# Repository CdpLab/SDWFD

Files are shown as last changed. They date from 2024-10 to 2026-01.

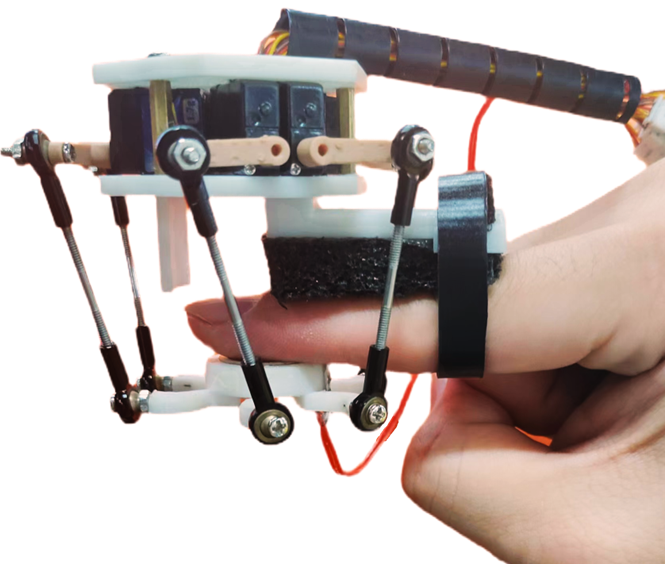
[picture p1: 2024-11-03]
picture/fig2b3.png

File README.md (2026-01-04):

<h1 align="center">Design and Evaluation of a 6-DoF Wearable Fingertip Device for Haptic Shape Rendering</h1>
<div align=center> 
Dapeng Chen, Da Yu, Yi Ding, Haojun Ni, Lifeng Zhu, Hong Zeng, Zhong Wei, Jia Liu, Aiguo Song 

Nanjing University of Information Science and Technology

---
</div>
CAD model, bill of materials and detailed manufacturing instructions, as well as its inverse kinematics and control code.The following two images show the CAD structural diagram and prototype of the device.
<div align=center>
Image text     Image text
</div>

The CAD structural diagram and prototype of the fingertip haptic device, including (A) mobile platform, (B) rocker arm, (C) fixed plate, (D) stop plate, (E) rigid link, (F) static platform, (G) steering engine, (H) rotating ball head, and (I) thin film pressure sensor.

## The CAD folder contains the assembly and various parts designed by our device.

Static platform: made of resin using 3D printing; Outer circle diameter: 48mm.

Mobile platform: made of resin using 3D printing; Outer circle diameter: 44mm, disc diameter: 22mm.

Rocker arm: Made of resin using 3D printing. Arm length: 13mm. Note: In the CAD folder, rocker arm 2 is used for 3D printing and comes with threads. And rocker arm 1 is only used for CAD display.

Rotating ball head: made of aluminum alloy.

Rigid link: made of aluminum alloy.

Screws and nuts: made of aluminum alloy.

Screw post: Made of brass.

Steering engine: Size: 16 × 17 × 6.2 mm³; mass: 17 g; model: SP017A-1; producer: DW Hobby; country: China.

Thin film pressure sensor: diameter: 20 mm; model: RP-C18.3-ST; producer: RunesKee; country: China.

## Installation process

First, install the steering engines onto the static platform. There are six square holes on the static platform to fix the rectangular prism protruding from the side of the steering engine and enhance its stability. Next, install the screw post at the corresponding position on the static platform. Then, install another static platform above the six steering engines, and securely connect two static platforms to the steering engines using screws and nuts. There is a circular hole designed on the static platform for the connection wire of the steering engine to pass through. Subsequently, the mobile platform and rigid link were installed, and the rotating ball head was pre installed in the rigid link. Connect the mobile platform to the rigid link through screws and nuts, with the screws passing through the rotating ball head. The other end of the rigid link is also connected to the rocker arm using this method, while the other end of the rocker arm is connected to the steering engine.

## Code
In the code section, we shared the code for the control, inverse kinematics, steering engine drive module, and membrane pressure sensor of the device. Among them, "FSR" is the code for the thin film pressure sensor, "control" is the code for device control, "inverse" is the code for inverse kinematics, and "pcA9685" is the code for the steering engine drive module.

## Demo video
The demonstration video can be viewed through the following link: https://youtu.be/AHHCAW3EiJQ .

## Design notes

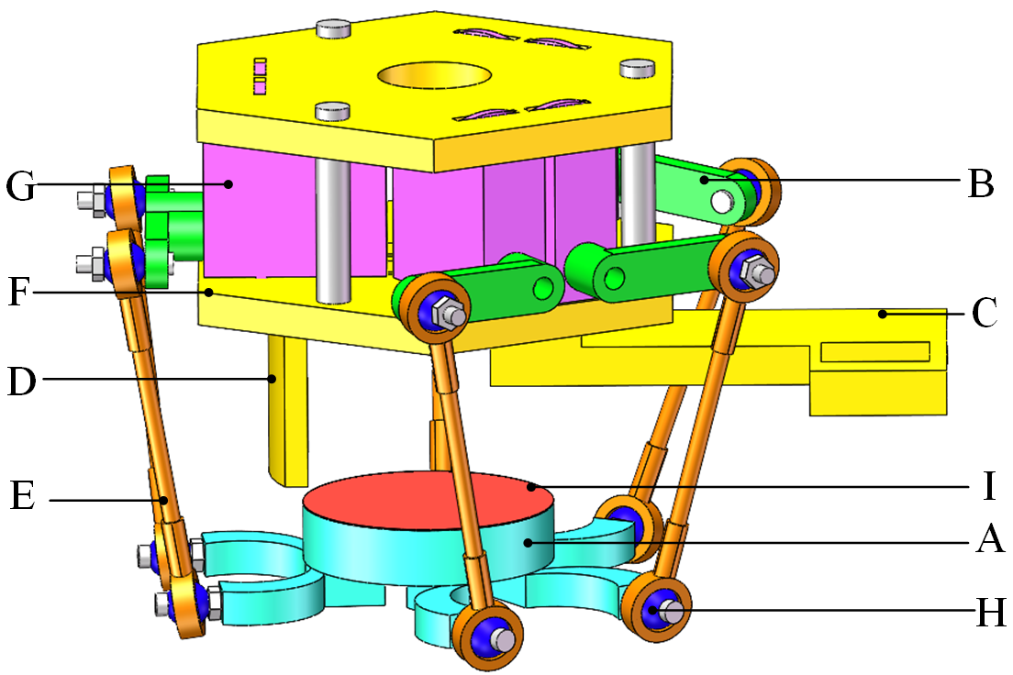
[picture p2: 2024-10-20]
picture/fig2a.png

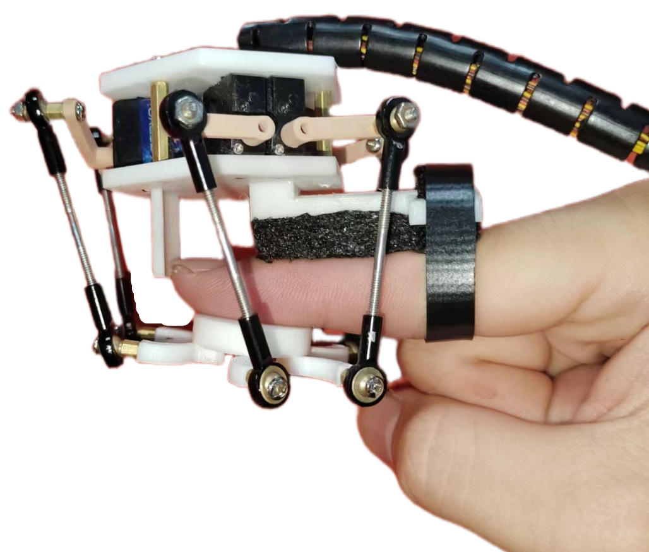
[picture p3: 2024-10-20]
picture/fig2b.png

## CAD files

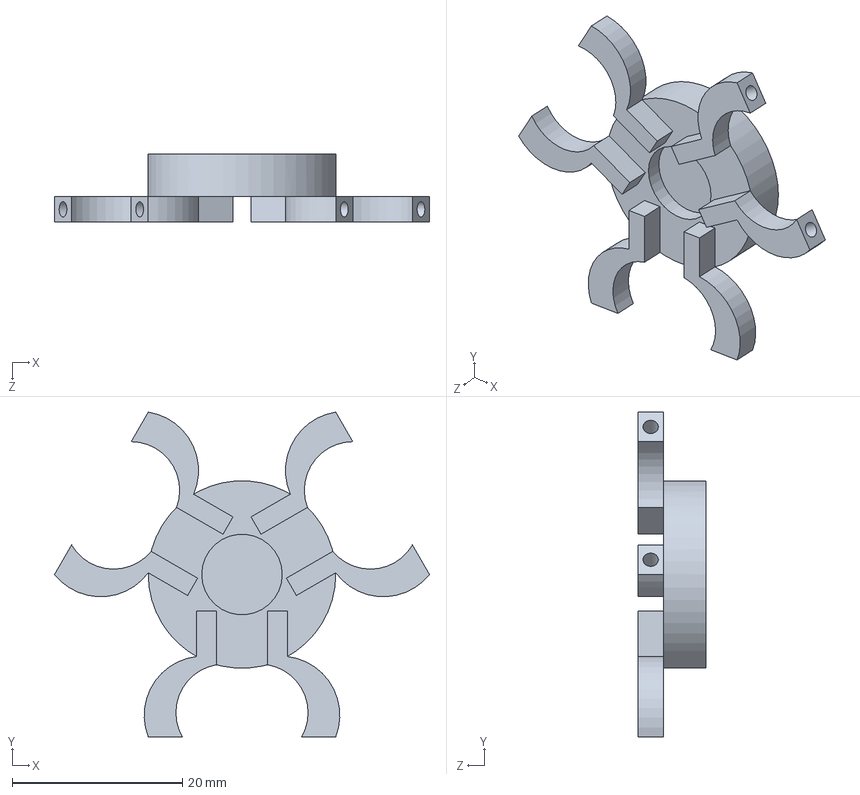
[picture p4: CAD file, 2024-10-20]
CAD/mobile platform.SLDPRT
44.0 x 38.1 x 8.00 mm

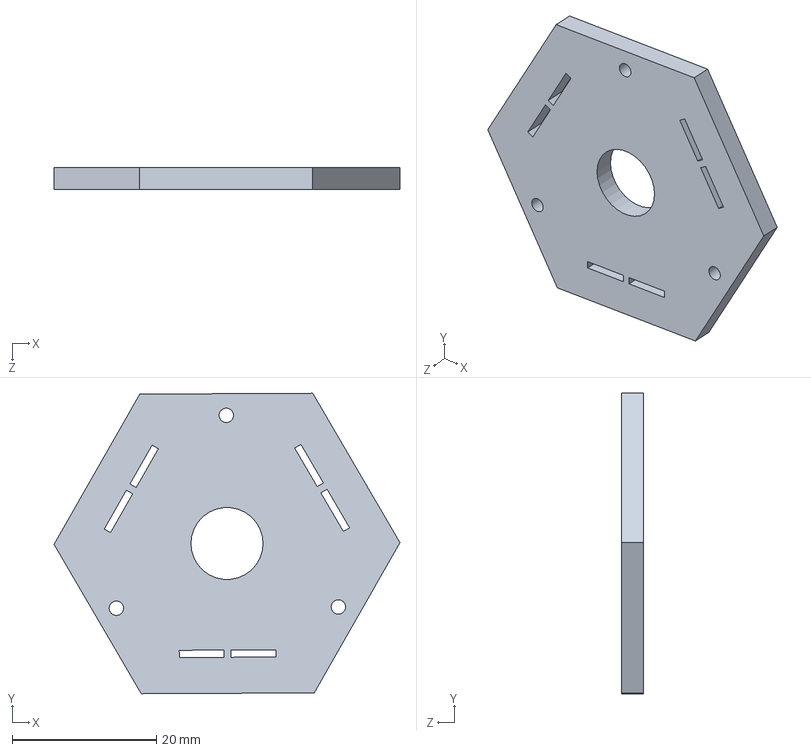
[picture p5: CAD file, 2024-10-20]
CAD/Static platform 2.SLDPRT
48.0 x 41.7 x 3.00 mm

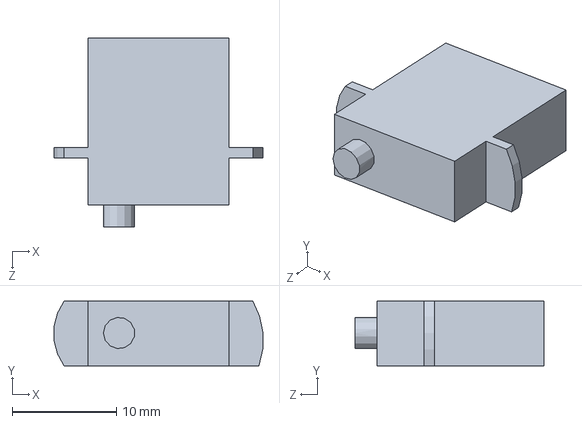
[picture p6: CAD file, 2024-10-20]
CAD/steering engine.SLDPRT
20.0 x 6.20 x 18.1 mm

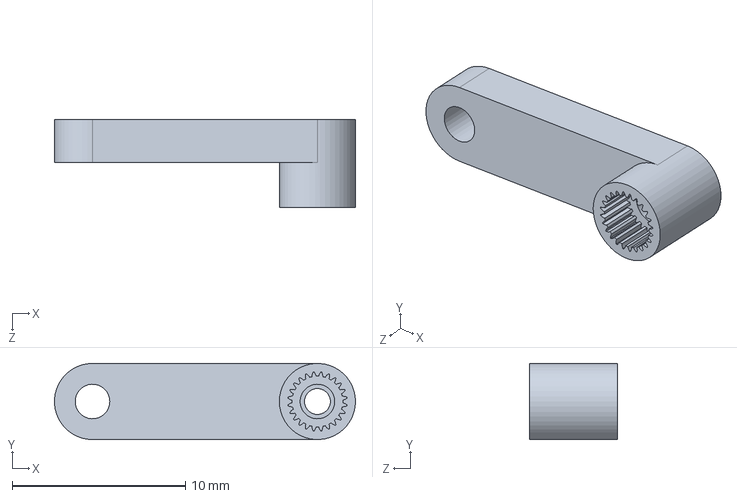
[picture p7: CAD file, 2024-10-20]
CAD/rocker arm2.SLDPRT
17.4 x 4.40 x 5.10 mm

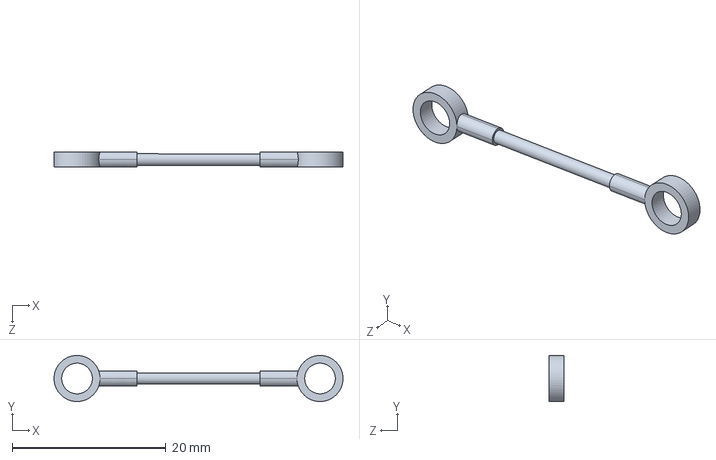
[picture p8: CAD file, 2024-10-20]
CAD/rigid link.SLDPRT
37.7 x 6.00 x 2.00 mm

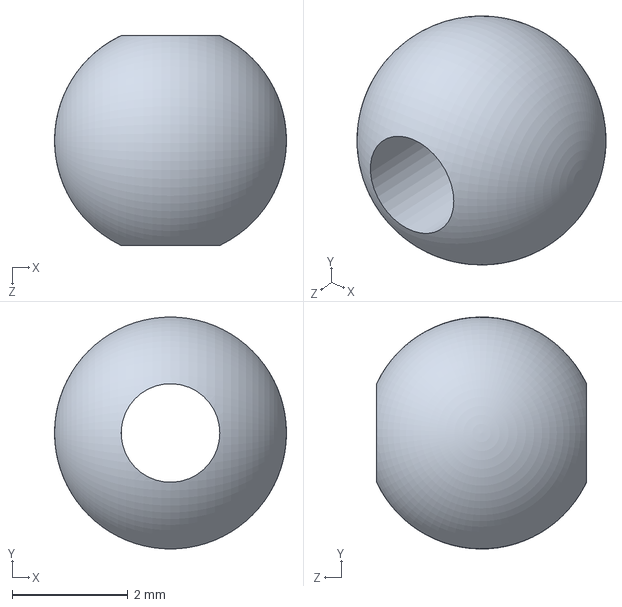
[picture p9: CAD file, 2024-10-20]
CAD/Rotating ball head.SLDPRT
4.00 x 4.00 x 3.62 mm

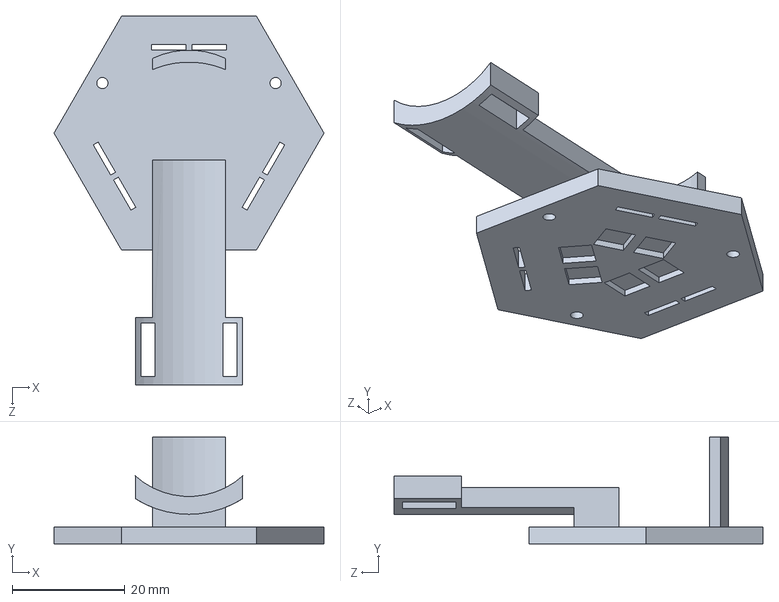
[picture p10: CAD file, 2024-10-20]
CAD/Static platform.SLDPRT
48.0 x 19.0 x 65.5 mm

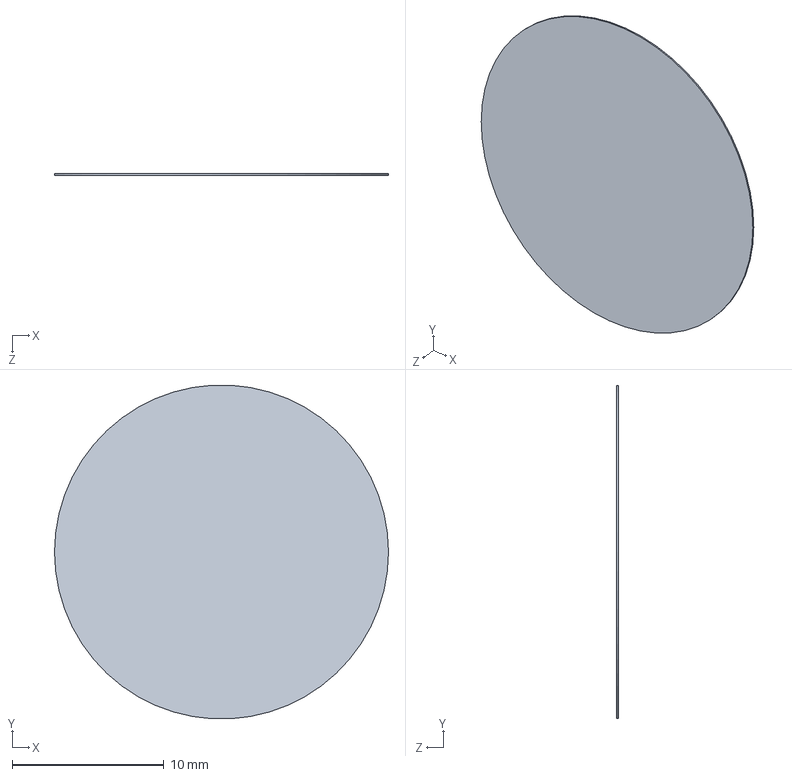
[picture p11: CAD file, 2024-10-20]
CAD/Thin film pressure sensor.SLDPRT
22.0 x 22.0 x 0.1 mm

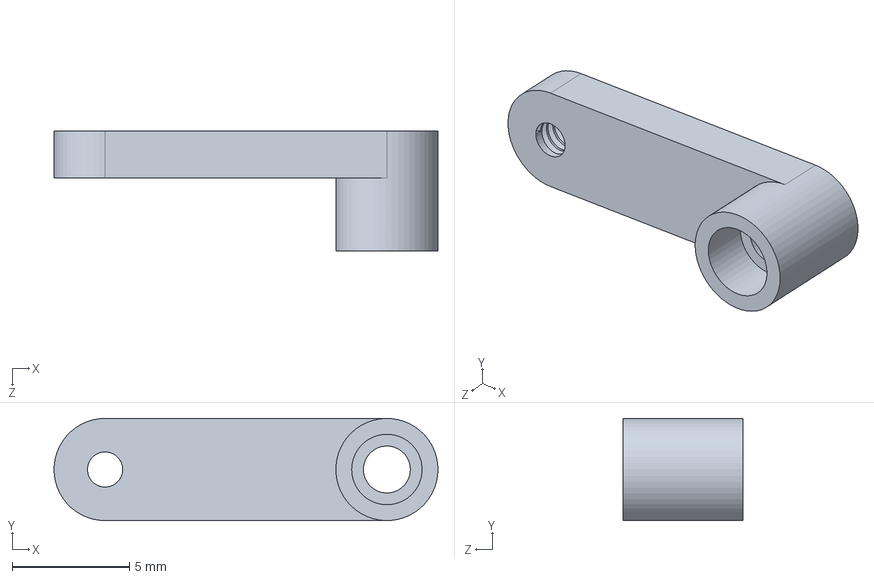
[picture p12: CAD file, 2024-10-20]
CAD/rocker arm.SLDPRT
16.4 x 4.35 x 5.10 mm

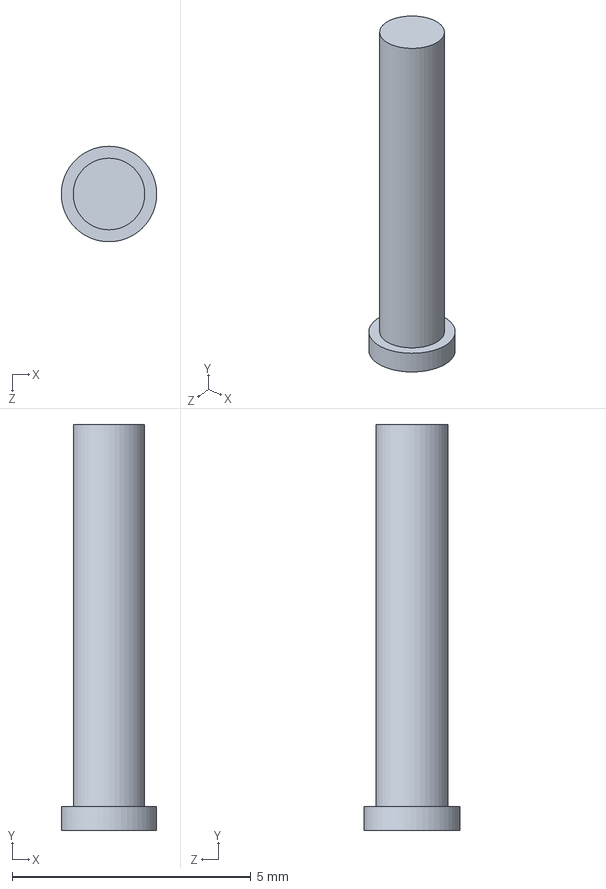
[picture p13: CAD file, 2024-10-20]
CAD/Screw 2.SLDPRT
2.00 x 8.50 x 2.00 mm

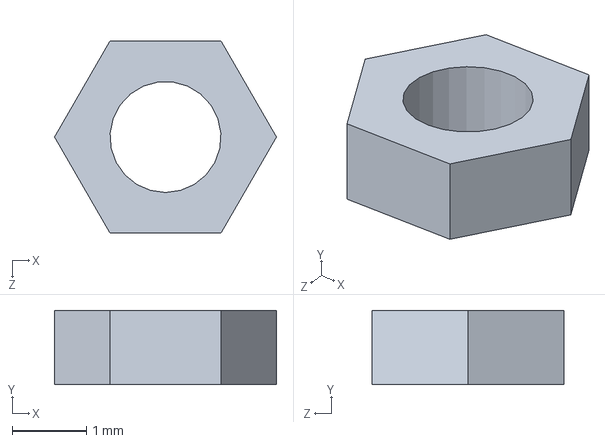
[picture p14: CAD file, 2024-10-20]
CAD/nut.SLDPRT
3.00 x 1.00 x 2.60 mm

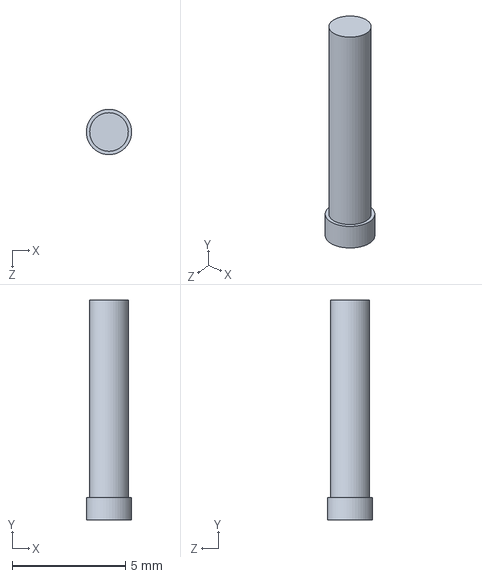
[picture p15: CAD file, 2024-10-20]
CAD/Screw.SLDPRT
2.00 x 9.70 x 2.00 mm

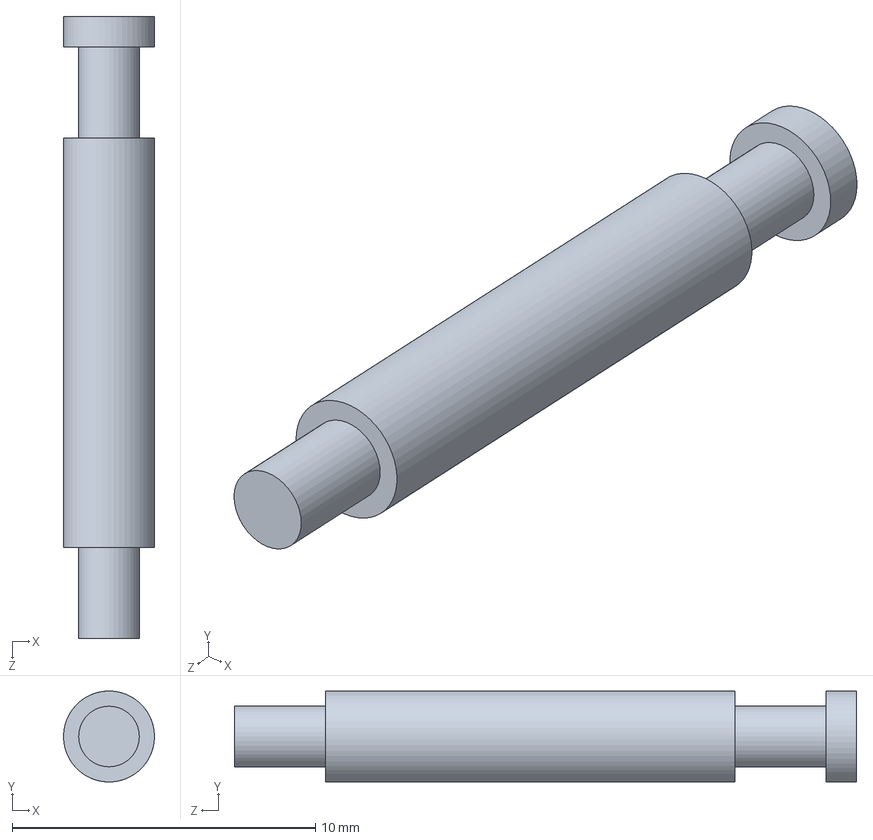
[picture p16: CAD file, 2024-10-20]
CAD/screw post.SLDPRT
3.00 x 3.00 x 20.5 mm

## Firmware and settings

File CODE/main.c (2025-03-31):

#include "system.h"
#include "SysTick.h"
#include "led.h"
#include "usart.h"
#include "FreeRTOS.h"
#include "task.h"
#include "key.h"
#include "limits.h"
#include "queue.h"
#include "serial.h"
#include "inverse.h"
#include "pca9685.h"
#include "adc.h"
#include "event_groups.h"
#include "semphr.h"
#include "limits.h"
#include "contorl.h"
//任务优先级
#define START_TASK_PRIO		1
//任务堆栈大小	
#define START_STK_SIZE 		128  
//任务句柄
TaskHandle_t StartTask_Handler;
//任务函数
void start_task(void *pvParameters);

//任务优先级
#define Inverse_task_PRIO		3
//任务堆栈大小	
#define Inverse_STK_SIZE 		128  
//任务句柄
TaskHandle_t Inversetask_Handler;
//任务函数
void Inverse_task(void *pvParameters);

//任务优先级
#define Controll_task_PRIO		4
//任务堆栈大小	
#define Controll_STK_SIZE 		50  
//任务句柄
TaskHandle_t Controlltask_Handler;
//任务函数
void Controll_task(void *pvParameters);

//任务优先级
#define Bluetooth_TASK_PRIO		2
//任务堆栈大小	
#define Bluetooth_STK_SIZE 		50  
//任务句柄
TaskHandle_t BluetoothTask_Handler;
//任务函数
void Bluetooth_task(void *pvParameters);

//任务优先级
#define FSR_TASK_PRIO		5
//任务堆栈大小	
#define FSR_STK_SIZE 		128  
//任务句柄
TaskHandle_t FSRTask_Handler;
//任务函数
void FSR_task(void *pvParameters);

#define  QUEUE_LEN    6   /* 队列的长度，最大可包含多少个消息 */
#define  QUEUE_SIZE   10   /* 队列中每个消息大小（字节） */
#define  Angel_LEN    6   /* 队列的长度，最大可包含多少个消息 */
#define  Angel_SIZE   10   /* 队列中每个消息大小（字节） */
#define  USE_CHAR  1  /* 测试字符串的时候配置为 1 ，测试变量配置为 0  */
#define PRESS_MAX	6000
#define PRESS_MIN	20
#define VOLTAGE_MIN 100
#define VOLTAGE_MAX 3300
#define KEY1_EVENT  (0x01 << 0)//设置事件掩码的位0
#define KEY2_EVENT  (0x01 << 1)//设置事件掩码的位1

QueueHandle_t Bluetooth_Queue =NULL;
QueueHandle_t Angel_Queue =NULL;
EventGroupHandle_t Event_Handle =NULL;
SemaphoreHandle_t MuxSem_Handle =NULL;
u16 adcBuffer[10];  
int main()
{
	SysTick_Init(72);
	NVIC_PriorityGroupConfig(NVIC_PriorityGroup_4);//设置系统中断优先级分组4
	LED_Init();
	KEY_Init();
	Servo_Init(50,60);
	USART1_Init(9600);
	Serial_Init();
   Adc_Init();
	//创建开始任务
    xTaskCreate((TaskFunction_t )start_task,            //任务函数
                (const char*    )"start_task",          //任务名称
                (uint16_t       )START_STK_SIZE,        //任务堆栈大小
                (void*          )NULL,                  //传递给任务函数的参数
                (UBaseType_t    )START_TASK_PRIO,       //任务优先级
                (TaskHandle_t*  )&StartTask_Handler);   //任务句柄              
    vTaskStartScheduler();          //开启任务调度
}

//开始任务任务函数
void start_task(void *pvParameters)
{
	taskENTER_CRITICAL();           //进入临界区
  /* 创建 Event_Handle */
	Event_Handle = xEventGroupCreate();
	/* 创建MuxSem */
	MuxSem_Handle = xSemaphoreCreateMutex();		
					
	xTaskCreate((TaskFunction_t )Bluetooth_task,     
                (const char*    )"Bluetooth_task",   
                (uint16_t       )Bluetooth_STK_SIZE, 
                (void*          )NULL,
                (UBaseType_t    )Bluetooth_TASK_PRIO,
                (TaskHandle_t*  )&BluetoothTask_Handler);					

		Bluetooth_Queue = xQueueCreate((UBaseType_t ) QUEUE_LEN,/* 消息队列的长度 */
                            (UBaseType_t ) QUEUE_SIZE);/* 消息的大小 */				
	
		Angel_Queue = xQueueCreate((UBaseType_t ) Angel_LEN,/* 消息队列的长度 */
                            (UBaseType_t ) Angel_SIZE);/* 消息的大小 */														
	/	
	xTaskCreate((TaskFunction_t )Inverse_task,     
                (const char*    )"Inverse_task",   
                (uint16_t       )Inverse_STK_SIZE, 
                (void*          )NULL,
                (UBaseType_t    )Inverse_task_PRIO,
                (TaskHandle_t*  )&Inversetask_Handler);					
		
	xTaskCreate((TaskFunction_t )Controll_task,     
                (const char*    )"Controll_task",   
                (uint16_t       )Controll_STK_SIZE, 
                (void*          )NULL,
                (UBaseType_t    )Controll_task_PRIO,
                (TaskHandle_t*  )&Controlltask_Handler);			
		
	xTaskCreate((TaskFunction_t )FSR_task,     
                (const char*    )"FSR_task",   
                (uint16_t       )FSR_STK_SIZE, 
                (void*          )NULL,
                (UBaseType_t    )FSR_TASK_PRIO,
                (TaskHandle_t*  )&FSRTask_Handler);							
    vTaskDelete(StartTask_Handler); //删除开始任务
    taskEXIT_CRITICAL();            //退出临界区
} 

void Bluetooth_task(void *pvParameters) {
    uint16_t t1;
    double xx[6];
    uint16_t t2 = 0;
 BaseType_t xReturn = pdPASS;/* 定义一个创建信息返回值，默认为pdPASS */
    while (1) {
        if (Serial_GetRxFlag() == 1) {
            t1 = Serial_GetRxData();
            xx[t2] = (double)t1;
            t2++;
            if (t2 == 6) { 
							xReturn = xSemaphoreTake(MuxSem_Handle,/* 互斥量句柄 */
                              portMAX_DELAY); /* 等待时间 */
							xQueueSend(Bluetooth_Queue, xx, 0);
                t2 = 0; 
        xEventGroupSetBits(Event_Handle,KEY1_EVENT); 
		    xReturn = xSemaphoreGive( MuxSem_Handle );//给出互斥量					
            }
        }
				vTaskDelay(20);
    }	
}

void Inverse_task(void *pvParameters) {
  BaseType_t xReturn = pdTRUE;/* 定义一个创建信息返回值，默认为pdTRUE */
	double rxData[6];	/* 定义一个接收消息的变量 */
	double *result;
	EventBits_t r_event;  /* 定义一个事件接收变量 */
	while(1)
    {
			  r_event = xEventGroupWaitBits(Event_Handle,  /* 事件对象句柄 */
                                  KEY1_EVENT|KEY2_EVENT,/* 接收线程感兴趣的事件 */
                                  pdTRUE,   /* 退出时清除事件位 */
                                  pdFALSE,   /* 满足感兴趣的所有事件 */
                                  portMAX_DELAY);/* 指定超时事件,一直等 */
			
     xReturn = xQueueReceive( Bluetooth_Queue,    /* 消息队列的句柄 */
								rxData,      /* 发送的消息内容 */
								portMAX_DELAY); /* 等待时间 一直等 */
		if(pdTRUE == xReturn){
			result = inv(rxData[0], rxData[1], rxData[2], rxData[3], rxData[4], rxData[5]);
//		  xQueueSend(Angel_Queue, result, 0);
			xReturn = xTaskNotify(Controll_task, /*任务句柄*/
								(uint32_t)&result, /* 发送的数据，最大为4字节 */
								eSetValueWithOverwrite );/*覆盖当前通知*/
		}
		else
			printf("数据接收出错,错误代码0x%lx\n",xReturn);
    }
}

void Controll_task(void *pvParameters) {
    BaseType_t xReturn = pdTRUE;/* 定义一个创建信息返回值，默认为pdTRUE */
	double *alpha1;
    while (1) {
			xReturn=xTaskNotifyWait(0x0,			//进入函数的时候不清除任务bit
								ULONG_MAX,	  //退出函数的时候清除所有的bit
								(uint32_t *)&alpha1,		  //保存任务通知值                       
								portMAX_DELAY);	//阻塞时间
			
//                xReturn = xQueueReceive( Angel_Queue,    /* 消息队列的句柄 */
//								alpha1,      /* 发送的消息内容 */
//								portMAX_DELAY); /* 等待时间 一直等 */
		if(pdTRUE == xReturn){
			//Servo_angle(10,60-(alpha1[0]));//-
		//Servo_angle(11,60+alpha1[1]);//+
		//Servo_angle(12,60-(alpha1[2]));
		//Servo_angle(13,60+(alpha1[3]));
		//Servo_angle(14,60-(alpha1[4])); 
		//Servo_angle(15,60+(alpha1[5]));
			servocontrol11(alpha1);
		}
		else
		{printf("数据接收出错,错误代码0x%lx\n",xReturn);}
			vTaskDelay(20);
            }
        }
				
void FSR_task(void *pvParameters) {
uint8_t state = 0;
uint16_t val = 0;
uint16_t value_AD = 0;
long PRESS_AO = 0;
uint16_t VOLTAGE_AO = 0;
BaseType_t xReturn = pdTRUE;/* 定义一个创建信息返回值，默认为pdTRUE */
	double zero[6]={0};
    while (1) {     
            value_AD = average(adcBuffer,10);	
		VOLTAGE_AO = map(value_AD, 0, 4095, 0, 3300);
		if(VOLTAGE_AO < VOLTAGE_MIN)
		{
			PRESS_AO = 0;
		}
		else if(VOLTAGE_AO > VOLTAGE_MAX)
		{
			PRESS_AO = PRESS_MAX;
		}
		else
		{
			PRESS_AO = map(VOLTAGE_AO, VOLTAGE_MIN, VOLTAGE_MAX, PRESS_MIN, PRESS_MAX);
			if (PRESS_AO>2500)
			{  xReturn = xSemaphoreTake(MuxSem_Handle,/* 互斥量句柄 */
                              portMAX_DELAY); /* 等待时间 */
				 xQueueSend(Bluetooth_Queue, zero, 0);
				 xEventGroupSetBits(Event_Handle,KEY2_EVENT);
				 xReturn = xSemaphoreGive( MuxSem_Handle);
			}
		}   
      vTaskDelay(20);		
		}
            }
        

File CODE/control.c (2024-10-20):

#include "stm32f10x.h"
#include "delay.h"
#include "sys.h"
#include "pca9685.h"
#include "usart.h"
#include "stdio.h"
#include "stdlib.h"
#include "string.h"
#include <stdarg.h>
#include "inverse.h"
#include "math.h"
#include "serial.h"
#include "MPU6050.h"
#include "inv_mpu.h"
#include "inv_mpu_dmp_motion_driver.h" 
#include "FSR.h"
#define NUM_SERVOS 6
#define INCREMENT 1.0  // 每次更新的角度增量
#define TOLERANCE 1
#define DELAY_MS 20  // 延迟时间

//差分法参数	
double timestep = 0.009;
double a0; double a1; double a2; double a3;double a4; double a5;
double omegaf;double omegai; double acci; double accf;
double tf = 0.8;
double thetai=45; double thetaf=135;
double theta0;double omega0;double acc0;
double t=0; 
int i = 0;
	
u8 state = 0;	
	
double *x;
double aa[6];
uint8_t RxData;
double val1 = 180 / 3.1415926;
int i1=0;
		int i2=0;
		double xx[24];
		uint8_t  yy[4];
    int  t1;
		double y1;
		int t2;
		double current_angles[NUM_SERVOS] = {60, 60, 60, 60, 60, 60};  // 初始化为当前角度
 int servo_pins[6] = {4, 7, 8, 11, 12, 15};			
	static u8 current_angle[6] = {0,0,0,0,0,0};	





//			for ( t = 0; t <= tf; t += timestep) {
//    thetai=60; thetaf=120;
//    omegai = 35; omegaf = 125;
//    acci = 20; accf = 40;
//    // 计算插值系数
//    a0 = thetai;
//    a1 = omegai;
//    a2 = acci/2;
//    a3 = (20*thetaf-20*thetai-(8*omegaf+12*omegai)*tf-(3*acci-accf)*(pow(tf,2))) / (2*(pow(tf,3)));
//    a4 = (30*thetai-30*thetaf+(14*omegaf+16*omegai)*tf+(3*acci-2*accf)*(pow(tf,2))) / (2*(pow(tf,4)));
//    a5 = (12*thetaf - 12*thetai - (6*omegaf+6*omegai)*tf-(acci-accf)*(pow(tf,2))) / (2*(pow(tf,5)));
//    // 计算当前时刻的角度、角速度和角加速度
//    theta0 = a0 +a1*t +a2*(pow(t,2))+ a3*(pow(t,3)) + a4*(pow(t,4)) + a5*(pow(t,5));
//    omega0 = a1 + 2*a2*t + 3*a3*(pow(t,2)) + 4*a4*(pow(t,3)) + 5*a5*(pow(t,4));
//    acc0 = 2*a2 + 6*a3*t + 12*a4*(pow(t,2)) + 20*a5*(pow(t,3));
//    // 设置舵机角度
//    Servo_angle(4,theta0);





void servocontrol11(double *x) {
    int x_int[NUM_SERVOS];  // 新的整数数组

    // 将目标数组 x 中的浮点数转换为整数
    for (int i = 0; i < NUM_SERVOS; i++) {
        x_int[i] = (int)round(x[i]);  // 使用 round 将浮点数四舍五入，并转为 int 类型
    }

		for (int i = 0; i < 6; i++) {
    if (x_int[i] < -60) {
        x_int[i] = -60; // 如果角度小于 -60，则截断为 -60
    } else if (x_int[i] > 60) {
        x_int[i] = 60; // 如果角度大于 60，则截断为 60
}
		
    // 进入循环，直到所有角度都达到目标
    int reached[NUM_SERVOS] = {0};  // 标记每个舵机是否达到目标
    while (1) {
        int all_reached = 1;  // 标记是否所有舵机都达到目标

        for (int i = 0; i < NUM_SERVOS; i++) {
            if (!reached[i]) {
                // 如果 current_angle[i] 和 x_int[i] 不相等，更新角度并控制舵机
                if (current_angle[i] < x_int[i]) {
                    current_angle[i]++;
                } else if (current_angle[i] > x_int[i]) {
                    current_angle[i]--;
                }

                // 当角度发生变化时，控制舵机
                if (i % 2 == 0) {  // i 是偶数
                    Servo_angle(servo_pins[i], 60 - current_angle[i]);
                } else {  // i 是奇数
                    Servo_angle(servo_pins[i], 60 + current_angle[i]);
                }

                // 检查是否已经达到目标角度
                if (abs(current_angle[i] - x_int[i]) <= TOLERANCE) {
                    reached[i] = 1;  // 标记为已达到目标
                } else {
                    all_reached = 0;  // 有舵机未达到目标
                }
            }
        }

        // 如果所有舵机都达到目标角度，则退出循环
        if (all_reached) {
            break;
        }

        // 每次循环结束后，增加适当的延迟，避免舵机频繁更新
        delay_ms(DELAY_MS);
    }
}
